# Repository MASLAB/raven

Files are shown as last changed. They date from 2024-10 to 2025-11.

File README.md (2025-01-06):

# raven
Robot Hardware Controller

## Pcb
Color pallet works best with KiCad wDark theme

## Firmware
Built using cmake and all dependencies exist locally

Install build tools if you need to
```
sudo apt install ninja-build cmake gcc-arm-none-eabi
```

### Compiling
Compile from motor-hub folder
```
cmake . --preset=Release
cd Release
ninja
```

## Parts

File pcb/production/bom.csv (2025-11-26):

Designator | Footprint | Quantity | Value | LCSC Part #
C1 | C_Elec_8x6.2 | 1 | 100u | C178539
C10, C18, C30, C31, C34, C35, C36, C39, C7, C8 | 0402 | 10 | 100n | C1525
C11, C44 | 0402 | 2 | 220n | C16772
C12 | 0603 | 1 | 4u7 | C19666
C13, C50, C51, C52, C53, C54, C57, C58, C59, C60, C61, C62, C63, C64, C65 | 0805 | 15 | 22u | C45783
C14, C16, C19, C2, C21, C24, C26, C4, C66, C68 | 0402 | 10 | 100n | C307331
C15, C20, C25, C3, C6, C67, C9 | 0402 | 7 | 2u2 | C12530
C17, C22, C27, C5, C69 | 0402 | 5 | 22n | C1532
C23 | 0603 | 1 | 100n | C14663
C28 | 0603 | 1 | 10u | C96446
C32, C33 | 0402 | 2 | 12p | C1547
C37, C38, C46, C47, C48, C49 | 0402 | 6 | 1u | C52923
C40, C41, C42, C43 | 1206 | 4 | 47u | C96123
C45 | 0805 | 1 | 2u2 | C377773
C55 | 0402 | 1 | 10u | C15525
D1, D12, D14, D27, D3, D6, D9 | 0603 | 7 | GLED | C72043
D10, D13, D28, D4, D7 | 0603 | 5 | RLED | C2286
D11, D2, D26, D5, D8 | 0603 | 5 | WLED | C2290
F1 | 1206 | 1 | Fuse | C2838917
FB1 | 0805 | 1 | FerriteBead | C1017
J2, J5 | JST_SH_SM04B-SRSS-TB_1x04-1MP_P1.00mm_Horizontal | 2 | Conn_01x04_MountingPin | C160404
L1 | L_0660A | 1 | 1u | C18199443
Q1 | SOT-23 | 1 | AO3400A | C20917
Q3 | DMP2002UPS | 1 | DMP2002UPS | C154869
R1, R10, R11, R12, R13, R14, R15, R16, R17, R18, R19, R2, R20, R21, R22, R23, R27, R3, R4, R5, R50, R59, R6, R60, R61, R62, R63, R9 | 0402 | 28 | 1k | C11702
R24 | 0402 | 1 | 33k | C25779
R25, R26, R28, R29, R31, R33, R34, R35, R37, R39, R40, R41, R43, R49, R51, R52, R54, R55, R66, R7, R8 | 0402 | 21 | 7k5 | C25918
R53, R57 | 0402 | 2 | 56k | C25796
R56 | 0402 | 1 | 47k | C25792
R58 | 0402 | 1 | 100k | C25741
SW1, SW2 | TS-1088 | 2 | SW_Push | C720477
U1, U30, U4, U5, U6 | HTSSOP-16-1EP_4.4x5mm_P0.65mm_EP3.4x5mm_Mask2.46x2.31mm | 5 | DRV8874PWPR | C1855818
U2 | LGA-14_3x2.5mm_P0.5mm_LayoutBorder3x4y | 1 | ICM-42688-P | C1850418
U7 | QFN-48-1EP_7x7mm_P0.5mm_EP5.6x5.6mm | 1 | STM32G431CBUx | C529356
U8 | SOIC-16_3.9x9.9mm_P1.27mm | 1 | 74HC595 | C5947
U9 | TPS548B28RWWR | 1 | TPS548B28RWWR | C3188716
Y1 | Crystal_SMD_3225-4Pin_3.2x2.5mm | 1 | 16MHz | C13738

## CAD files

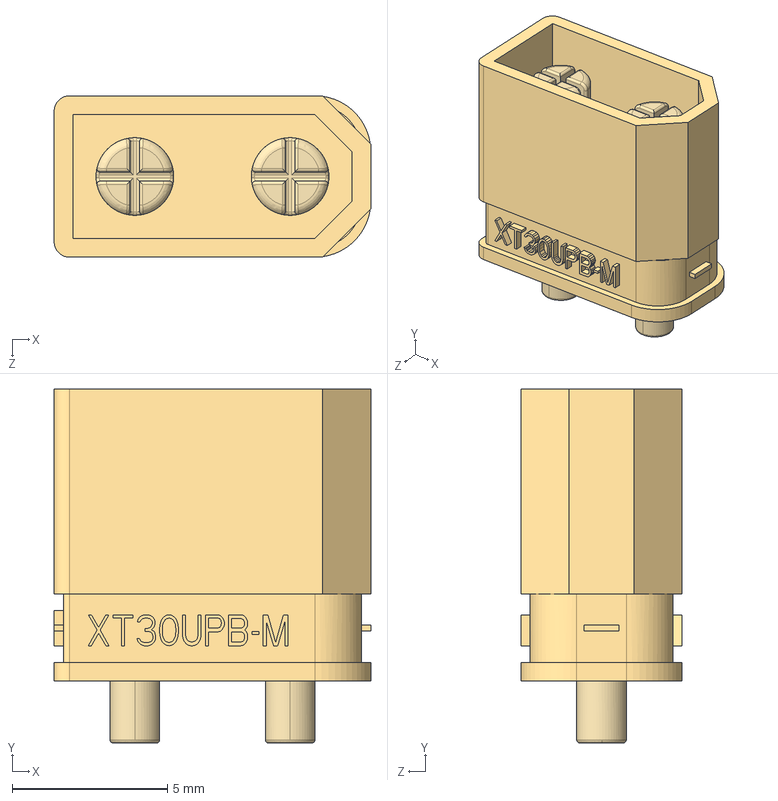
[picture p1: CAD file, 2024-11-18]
pcb/3dmodels/XT30UPB-M.STEP
10.2 x 11.4 x 5.20 mm
XT30UPB-M
XT30UPB-M-PIN x 2

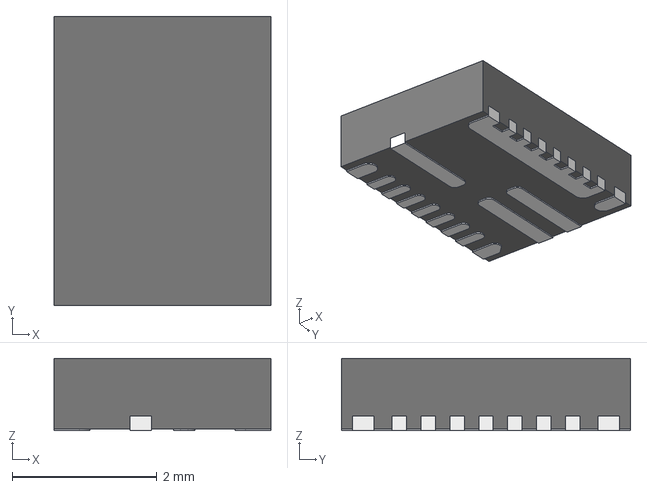
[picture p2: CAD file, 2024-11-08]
pcb/3dmodels/RWW0021A.STEP
3.00 x 4.00 x 1.00 mm
FRAME
MOLD

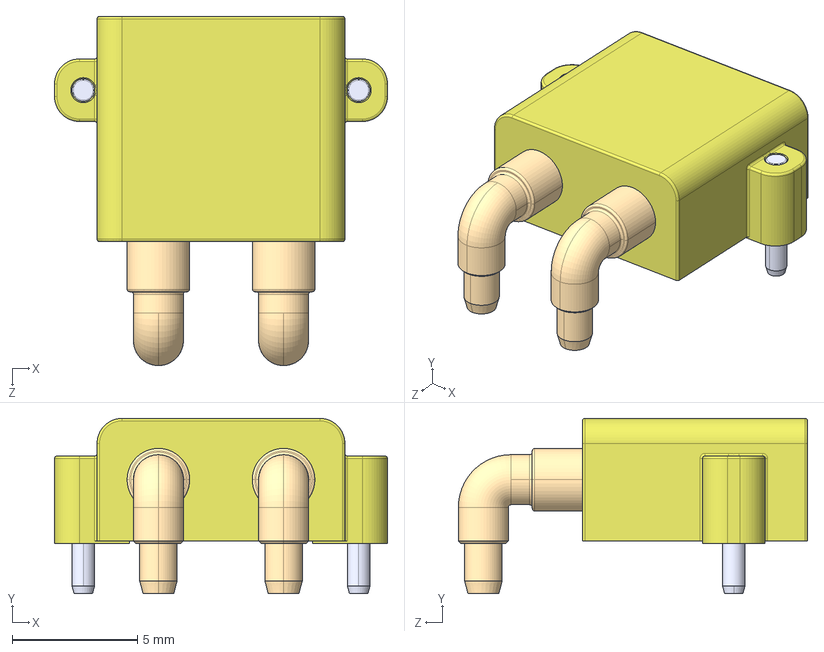
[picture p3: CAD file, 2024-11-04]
pcb/3dmodels/XT30PW-M.STEP
13.3 x 7.00 x 14.0 mm

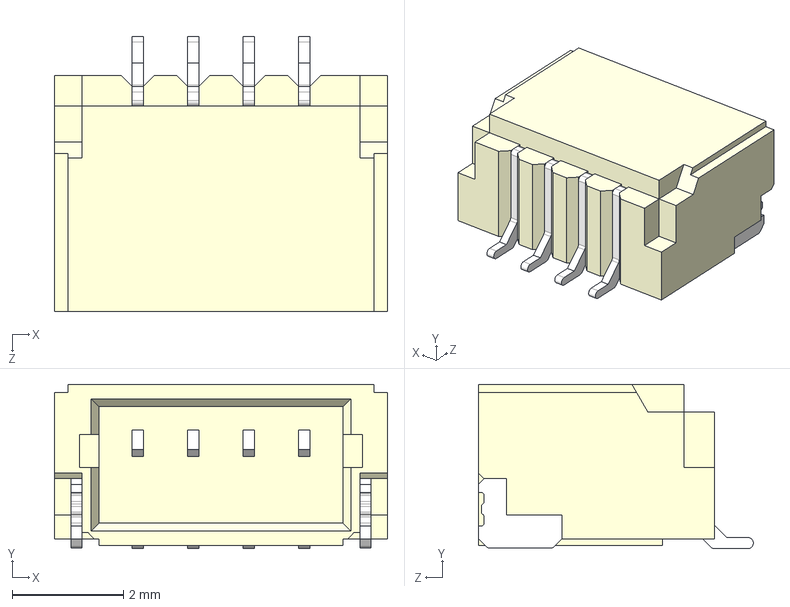
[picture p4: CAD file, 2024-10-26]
pcb/3dmodels/SM04B-SRSS-TB.STEP
6.00 x 2.96 x 4.95 mm

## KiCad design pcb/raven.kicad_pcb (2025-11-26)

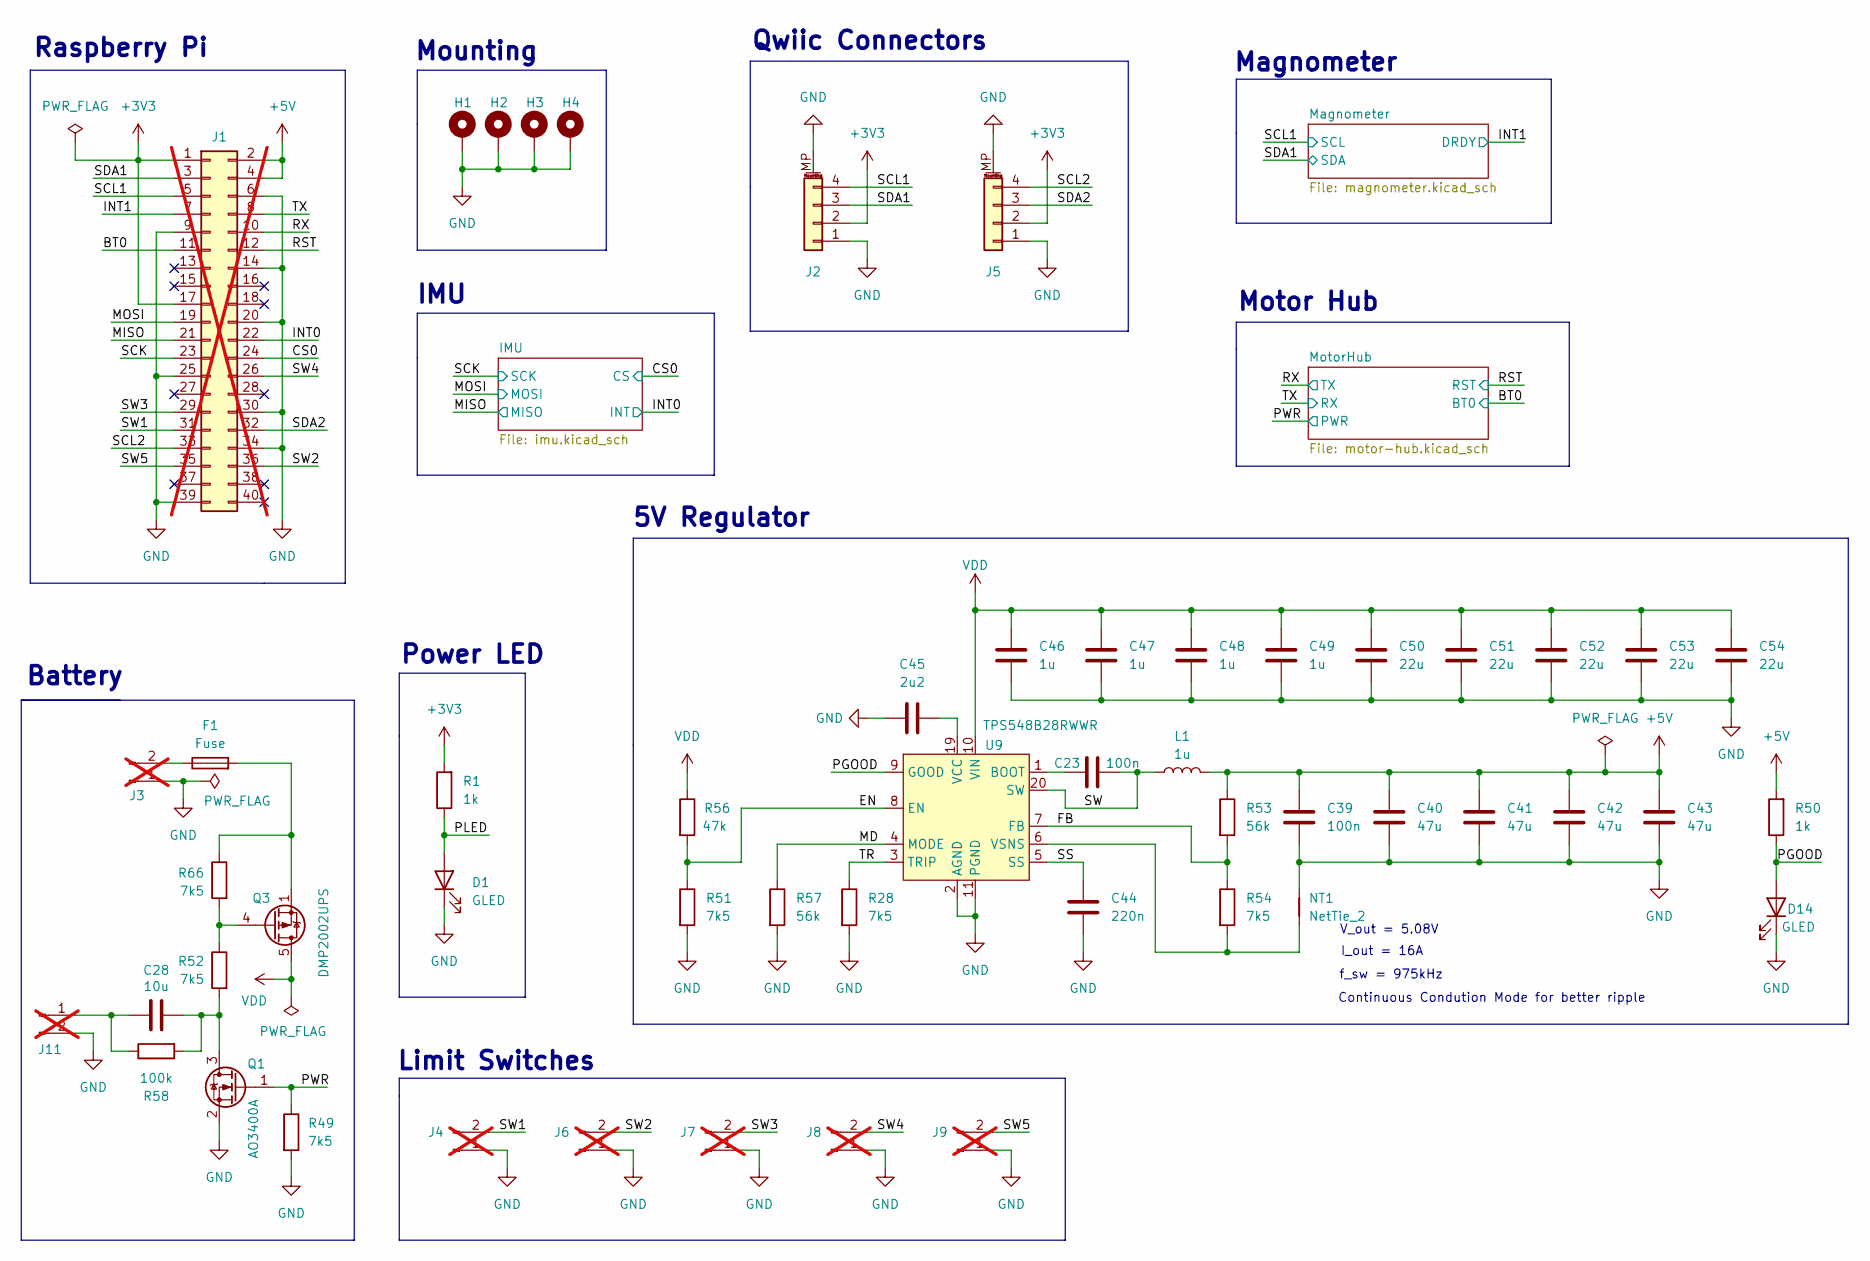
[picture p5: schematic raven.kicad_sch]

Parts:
C23: 100n; C_0603_1608Metric; LCSC C14663
C28: 10u; C_0603_1608Metric; LCSC C96446
C39: 100n; C_0402_1005Metric; LCSC C1525
C40, C41, C42, C43: 47u; C_1206_3216Metric; LCSC C96123
C44: 220n; C_0402_1005Metric; LCSC C16772
C45: 2u2; C_0805_2012Metric; LCSC C377773
C46, C47, C48, C49: 1u; C_0402_1005Metric; LCSC C52923
C50, C51, C52, C53, C54: 22u; C_0805_2012Metric; LCSC C45783
D1, D14: GLED; LED_0603_1608Metric; LCSC C72043
F1: Fuse; Fuse_1206_3216Metric; LCSC C2838917
H1, H2, H3, H4: MountingHole_Pad; MountingHole_2.5mm_Pad
J1: Conn_02x20_Odd_Even; PinSocket_2x20_P2.54mm_Vertical; LCSC C35165; not fitted
J2, J5: Conn_01x04_MountingPin; JST_SH_SM04B-SRSS-TB_1x04-1MP_P1.00mm_Horizontal; LCSC C160404
J3: Conn_01x02_Pin; AMASS_XT30UPB-M_1x02_P5.0mm_Vertical; LCSC C428721; not fitted
J4, J6, J7, J8, J9: Conn_01x02_Pin; PinHeader_1x02_P2.54mm_Vertical; LCSC C492401; not fitted
J11: Conn_01x02_Pin; JST_PH_B2B-PH-K_1x02_P2.00mm_Vertical; LCSC C131337; not fitted
L1: 1u; L_0660A; LCSC C18199443
NT1: NetTie_2; NetTie-2_SMD_Pad0.5mm
Q1: AO3400A; SOT-23; LCSC C20917
Q3: DMP2002UPS; LCSC C154869
R1, R50: 1k; R_0402_1005Metric; LCSC C11702
R28, R49, R51, R52, R54, R66: 7k5; R_0402_1005Metric; LCSC C25918
R53, R57: 56k; R_0402_1005Metric; LCSC C25796
R56: 47k; R_0402_1005Metric; LCSC C25792
R58: 100k; R_0402_1005Metric; LCSC C25741
U9: TPS548B28RWWR; LCSC C3188716

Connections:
+3V3: J1.1, J1.17, J2.2, J5.2, R1.2; also elsewhere on the board
+5V: C39.2, C40.1, C41.1, C42.1, C43.1, J1.2, J1.4, L1.2, R50.2, R53.1; also elsewhere on the board
/BT0: J1.11; also elsewhere on the board
/CS0: J1.24; also elsewhere on the board
/EN: R51.1, R56.2, U9.8 (EN)
/FB: R53.2, R54.1, U9.7 (FB)
/INT0: J1.22; also elsewhere on the board
/INT1: J1.7; also elsewhere on the board
/MD: R57.1, U9.4 (MODE)
/MISO: J1.21; also elsewhere on the board
/MOSI: J1.19; also elsewhere on the board
/PGOOD: D14.2 (A), R50.1, U9.9 (GOOD)
/PLED: D1.2 (A), R1.1
/PWR: Q1.1 (G), R49.1; also elsewhere on the board
/RST: J1.12; also elsewhere on the board
/RX: J1.10; also elsewhere on the board
/SCK: J1.23; also elsewhere on the board
/SCL1: J1.5, J2.4; also elsewhere on the board
/SCL2: J1.33, J5.4
/SDA1: J1.3, J2.3; also elsewhere on the board
/SDA2: J1.32, J5.3
/SS: C44.1, U9.5 (SS)
/SW: C23.2, L1.1, U9.20 (SW)
/SW1: J1.31, J4.2
/SW2: J1.36, J6.2
/SW3: J1.29, J7.2
/SW4: J1.26, J8.2
/SW5: J1.35, J9.2
/TR: R28.1, U9.3 (TRIP)
/TX: J1.8; also elsewhere on the board
GND: C39.1, C40.2, C41.2, C42.2, C43.2, C44.2, C45.1, C46.2, C47.2, C48.2, C49.2, C50.2, C51.2, C52.2, C53.2, C54.2, D1.1 (K), D14.1 (K), H1.1, H2.1, H3.1, H4.1, J1.6, J1.9, J1.14, J1.20, J1.25, J1.30, J1.34, J1.39, J2.1, J2.MP (MountPin), J3.1, J4.1, J5.1, J5.MP (MountPin), J6.1, J7.1, J8.1, J9.1, J11.2, NT1.1, Q1.2 (S), R28.2, R49.2, R51.2, R57.2, U9.2 (AGND), U9.11 (PGND), U9.12 (PGND), U9.13 (PGND), U9.14 (PGND), U9.15 (PGND), U9.16 (PGND), U9.17 (PGND), U9.18 (PGND); also elsewhere on the board
unnamed: F1.2, Q3.1 (S), Q3.2 (S), Q3.3 (S), R66.1
unnamed: F1.1, J3.2
unnamed: C28.1, J11.1, R58.1
unnamed: C28.2, Q1.3 (D), R52.2, R58.2
unnamed: Q3.4 (G), R52.1, R66.2
unnamed: C23.1, U9.1 (BOOT)
unnamed: C45.2, U9.19 (VCC)
unnamed: NT1.2, R54.2, U9.6 (VSNS)
VDD: C46.1, C47.1, C48.1, C49.1, C50.1, C51.1, C52.1, C53.1, C54.1, Q3.5 (D), Q3.6 (D), Q3.7 (D), Q3.8 (D), R56.1, U9.10 (VIN), U9.21 (VIN); also elsewhere on the board

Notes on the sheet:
Mounting
Power LED
5V Regulator
IMU
Motor Hub
V_out = 5.08V
Limit Switches
Continuous Condution Mode for better ripple
Qwiic Connectors
Battery
I_out = 16A
f_sw = 975kHz
Raspberry Pi
Magnometer

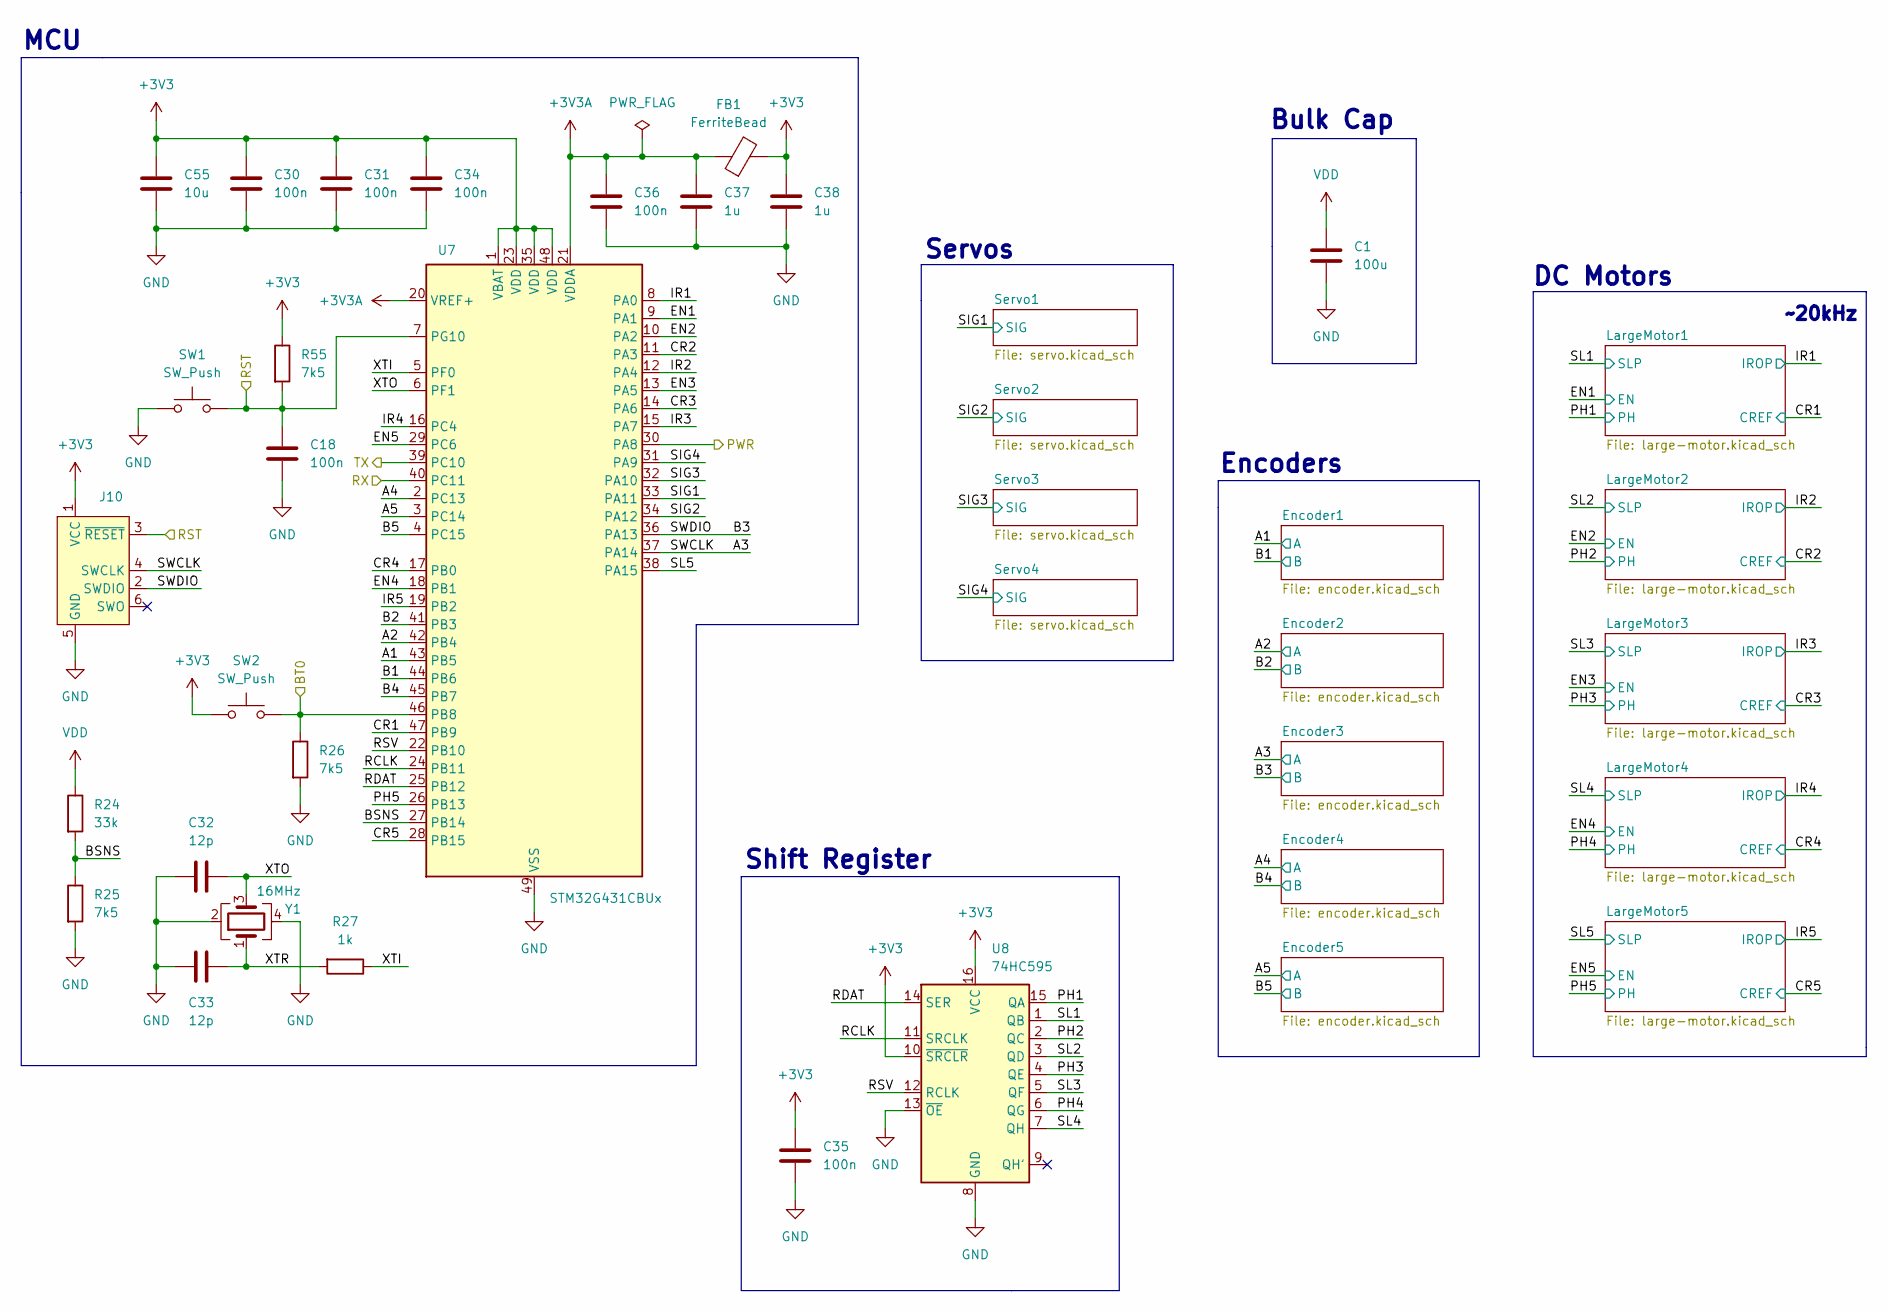
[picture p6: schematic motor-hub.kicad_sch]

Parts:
C1: 100u; C_Elec_8x6.2; LCSC C178539
C18, C30, C31, C34, C35, C36: 100n; C_0402_1005Metric; LCSC C1525
C32, C33: 12p; C_0402_1005Metric; LCSC C1547
C37, C38: 1u; C_0402_1005Metric; LCSC C52923
C55: 10u; C_0402_1005Metric; LCSC C15525
FB1: FerriteBead; L_0805_2012Metric; LCSC C1017
J10: Conn_ARM_SWD_TagConnect_TC2030-NL; Tag-Connect_TC2030-IDC-NL_2x03_P1.27mm_Vertical
R24: 33k; R_0402_1005Metric; LCSC C25779
R25, R26, R55: 7k5; R_0402_1005Metric; LCSC C25918
R27: 1k; R_0402_1005Metric; LCSC C11702
SW1, SW2: SW_Push; TS-1088; LCSC C720477
U7: STM32G431CBUx; QFN-48-1EP_7x7mm_P0.5mm_EP5.6x5.6mm; LCSC C529356
U8: 74HC595; SOIC-16_3.9x9.9mm_P1.27mm; LCSC C5947
Y1: 16MHz; Crystal_SMD_3225-4Pin_3.2x2.5mm; LCSC C13738

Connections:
+3V3: C30.1, C31.1, C34.1, C35.1, C38.1, C55.1, FB1.2, J10.1 (VCC), R55.1, SW2.1, U7.1 (VBAT), U7.23 (VDD), U7.35 (VDD), U7.48 (VDD), U8.10 (~SRCLR), U8.16 (VCC); also elsewhere on the board
+3V3A: C36.1, C37.1, FB1.1, U7.20 (VREF+), U7.21 (VDDA)
/BT0: R26.1, SW2.2, U7.46 (PB8); also elsewhere on the board
/MotorHub/A1: U7.43 (PB5); also elsewhere on the board
/MotorHub/A2: U7.42 (PB4); also elsewhere on the board
/MotorHub/A3: J10.4 (SWCLK), U7.37 (PA14); also elsewhere on the board
/MotorHub/A4: U7.2 (PC13); also elsewhere on the board
/MotorHub/A5: U7.3 (PC14); also elsewhere on the board
/MotorHub/B1: U7.44 (PB6); also elsewhere on the board
/MotorHub/B2: U7.41 (PB3); also elsewhere on the board
/MotorHub/B3: J10.2 (SWDIO), U7.36 (PA13); also elsewhere on the board
/MotorHub/B4: U7.45 (PB7); also elsewhere on the board
/MotorHub/B5: U7.4 (PC15); also elsewhere on the board
/MotorHub/BSNS: R24.2, R25.1, U7.27 (PB14)
/MotorHub/CR1: U7.47 (PB9); also elsewhere on the board
/MotorHub/CR2: U7.11 (PA3); also elsewhere on the board
/MotorHub/CR3: U7.14 (PA6); also elsewhere on the board
/MotorHub/CR4: U7.17 (PB0); also elsewhere on the board
/MotorHub/CR5: U7.28 (PB15); also elsewhere on the board
/MotorHub/EN1: U7.9 (PA1); also elsewhere on the board
/MotorHub/EN2: U7.10 (PA2); also elsewhere on the board
/MotorHub/EN3: U7.13 (PA5); also elsewhere on the board
/MotorHub/EN4: U7.18 (PB1); also elsewhere on the board
/MotorHub/EN5: U7.29 (PC6); also elsewhere on the board
/MotorHub/IR1: U7.8 (PA0); also elsewhere on the board
/MotorHub/IR2: U7.12 (PA4); also elsewhere on the board
/MotorHub/IR3: U7.15 (PA7); also elsewhere on the board
/MotorHub/IR4: U7.16 (PC4); also elsewhere on the board
/MotorHub/IR5: U7.19 (PB2); also elsewhere on the board
/MotorHub/PH1: U8.15 (QA); also elsewhere on the board
/MotorHub/PH2: U8.2 (QC); also elsewhere on the board
/MotorHub/PH3: U8.4 (QE); also elsewhere on the board
/MotorHub/PH4: U8.6 (QG); also elsewhere on the board
/MotorHub/PH5: U7.26 (PB13); also elsewhere on the board
/MotorHub/RCLK: U7.24 (PB11), U8.11 (SRCLK)
/MotorHub/RDAT: U7.25 (PB12), U8.14 (SER)
/MotorHub/RSV: U7.22 (PB10), U8.12 (RCLK)
/MotorHub/SIG1: U7.33 (PA11); also elsewhere on the board
/MotorHub/SIG2: U7.34 (PA12); also elsewhere on the board
/MotorHub/SIG3: U7.32 (PA10); also elsewhere on the board
/MotorHub/SIG4: U7.31 (PA9); also elsewhere on the board
/MotorHub/SL1: U8.1 (QB); also elsewhere on the board
/MotorHub/SL2: U8.3 (QD); also elsewhere on the board
/MotorHub/SL3: U8.5 (QF); also elsewhere on the board
/MotorHub/SL4: U8.7 (QH); also elsewhere on the board
/MotorHub/SL5: U7.38 (PA15); also elsewhere on the board
/MotorHub/XTI: R27.1, U7.5 (PF0)
/MotorHub/XTO: C32.2, U7.6 (PF1), Y1.3
/MotorHub/XTR: C33.2, R27.2, Y1.1
/PWR: U7.30 (PA8); also elsewhere on the board
/RST: C18.1, J10.3 (~RESET), R55.2, SW1.2, U7.7 (PG10); also elsewhere on the board
/RX: U7.39 (PC10); also elsewhere on the board
/TX: U7.40 (PC11); also elsewhere on the board
GND: C1.2, C18.2, C30.2, C31.2, C32.1, C33.1, C34.2, C35.2, C36.2, C37.2, C38.2, C55.2, J10.5 (GND), R25.2, R26.2, SW1.1, U7.49 (VSS), U8.8 (GND), U8.13 (~OE), Y1.2, Y1.4; also elsewhere on the board
VDD: C1.1, R24.1; also elsewhere on the board

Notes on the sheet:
~20kHz
Bulk Cap
Servos
MCU
DC Motors
Encoders
Shift Register

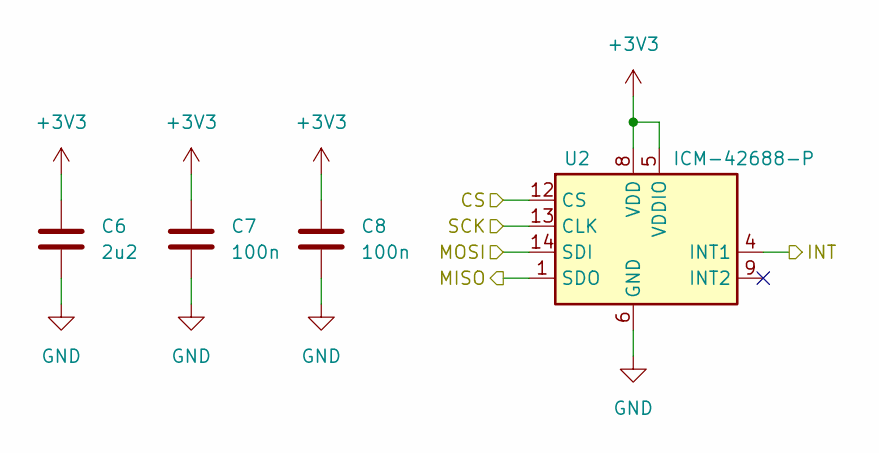
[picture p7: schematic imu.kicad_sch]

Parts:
C6: 2u2; C_0402_1005Metric; LCSC C12530
C7, C8: 100n; C_0402_1005Metric; LCSC C1525
U2: ICM-42688-P; LGA-14_3x2.5mm_P0.5mm_LayoutBorder3x4y; LCSC C1850418

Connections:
+3V3: C6.1, C7.1, C8.1, U2.5 (VDDIO), U2.8 (VDD); also elsewhere on the board
/CS0: U2.12 (CS); also elsewhere on the board
/INT0: U2.4 (INT1); also elsewhere on the board
/MISO: U2.1 (SDO); also elsewhere on the board
/MOSI: U2.14 (SDI); also elsewhere on the board
/SCK: U2.13 (CLK); also elsewhere on the board
GND: C6.2, C7.2, C8.2, U2.6 (GND), U2.7 (RESV), U2.11 (RESV); also elsewhere on the board

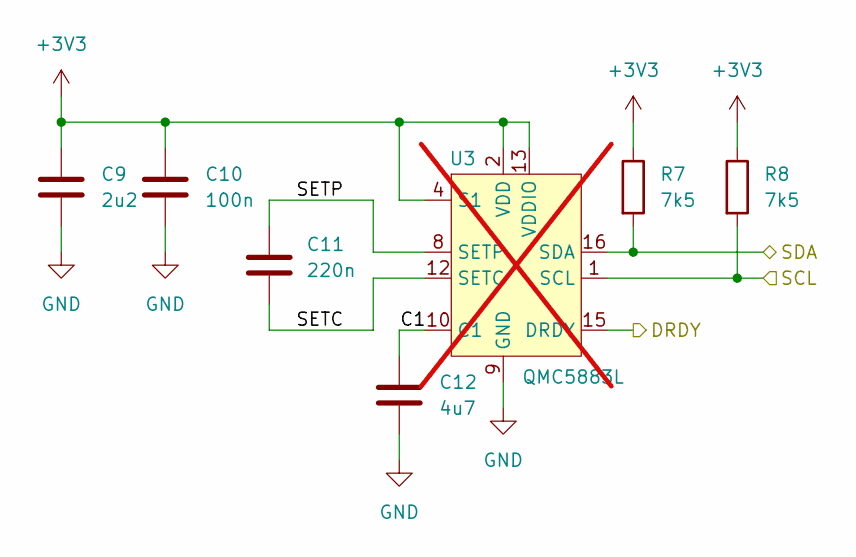
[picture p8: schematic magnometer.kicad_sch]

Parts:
C9: 2u2; C_0402_1005Metric; LCSC C12530
C10: 100n; C_0402_1005Metric; LCSC C1525
C11: 220n; C_0402_1005Metric; LCSC C16772
C12: 4u7; C_0603_1608Metric; LCSC C19666
R7, R8: 7k5; R_0402_1005Metric; LCSC C25918
U3: QMC5883L; LGA-16_3x3mm_P0.5mm; not fitted

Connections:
+3V3: C9.1, C10.1, R7.1, R8.1, U3.2 (VDD), U3.4 (S1), U3.13 (VDDIO); also elsewhere on the board
/INT1: U3.15 (DRDY); also elsewhere on the board
/Magnometer/C1: C12.1, U3.10 (C1)
/Magnometer/SETC: C11.2, U3.12 (SETC)
/Magnometer/SETP: C11.1, U3.8 (SETP)
/SCL1: R8.2, U3.1 (SCL); also elsewhere on the board
/SDA1: R7.2, U3.16 (SDA); also elsewhere on the board
GND: C9.2, C10.2, C12.2, U3.9 (GND), U3.11 (GND); also elsewhere on the board

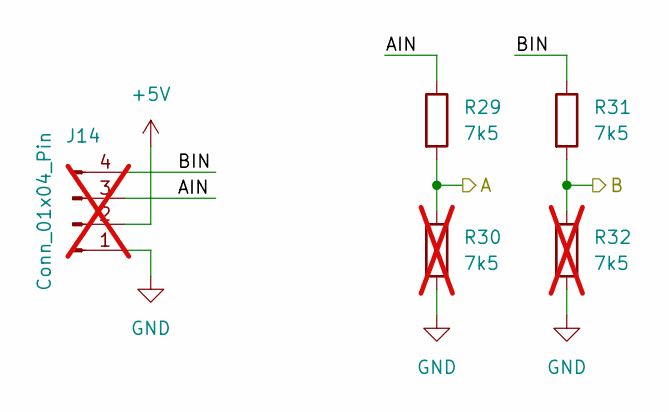
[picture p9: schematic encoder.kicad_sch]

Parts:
J14: Conn_01x04_Pin; PinHeader_1x04_P2.54mm_Vertical; LCSC C6332197; not fitted
R29, R31: 7k5; R_0402_1005Metric; LCSC C25918
R30, R32: 7k5; R_0402_1005Metric; LCSC C25918; not fitted

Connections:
+5V: J14.2; also elsewhere on the board
/MotorHub/A1: R29.2, R30.1; also elsewhere on the board
/MotorHub/B1: R31.2, R32.1; also elsewhere on the board
/MotorHub/Encoder1/AIN: J14.3, R29.1
/MotorHub/Encoder1/BIN: J14.4, R31.1
GND: J14.1, R30.2, R32.2; also elsewhere on the board

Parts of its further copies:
J15, J16, J17, J18: Conn_01x04_Pin; PinHeader_1x04_P2.54mm_Vertical; LCSC C6332197; not fitted
R33, R34, R35, R37, R39, R40, R41, R43: 7k5; R_0402_1005Metric; LCSC C25918
R36, R38, R42, R44, R45, R46, R47, R48: 7k5; R_0402_1005Metric; LCSC C25918; not fitted

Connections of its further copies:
+5V: J15.2, J16.2, J17.2, J18.2; also elsewhere on the board
/MotorHub/A2: R33.2, R36.1; also elsewhere on the board
/MotorHub/A3: R34.2, R42.1; also elsewhere on the board
/MotorHub/A4: R35.2, R47.1; also elsewhere on the board
/MotorHub/A5: R39.2, R48.1; also elsewhere on the board
/MotorHub/B2: R37.2, R38.1; also elsewhere on the board
/MotorHub/B3: R40.2, R44.1; also elsewhere on the board
/MotorHub/B4: R41.2, R45.1; also elsewhere on the board
/MotorHub/B5: R43.2, R46.1; also elsewhere on the board
/MotorHub/Encoder2/AIN: J15.3, R33.1
/MotorHub/Encoder2/BIN: J15.4, R37.1
/MotorHub/Encoder3/AIN: J16.3, R34.1
/MotorHub/Encoder3/BIN: J16.4, R40.1
/MotorHub/Encoder4/AIN: J17.3, R35.1
/MotorHub/Encoder4/BIN: J17.4, R41.1
/MotorHub/Encoder5/AIN: J18.3, R39.1
/MotorHub/Encoder5/BIN: J18.4, R43.1
GND: J15.1, J16.1, J17.1, J18.1, R36.2, R38.2, R42.2, R44.2, R45.2, R46.2, R47.2, R48.2; also elsewhere on the board

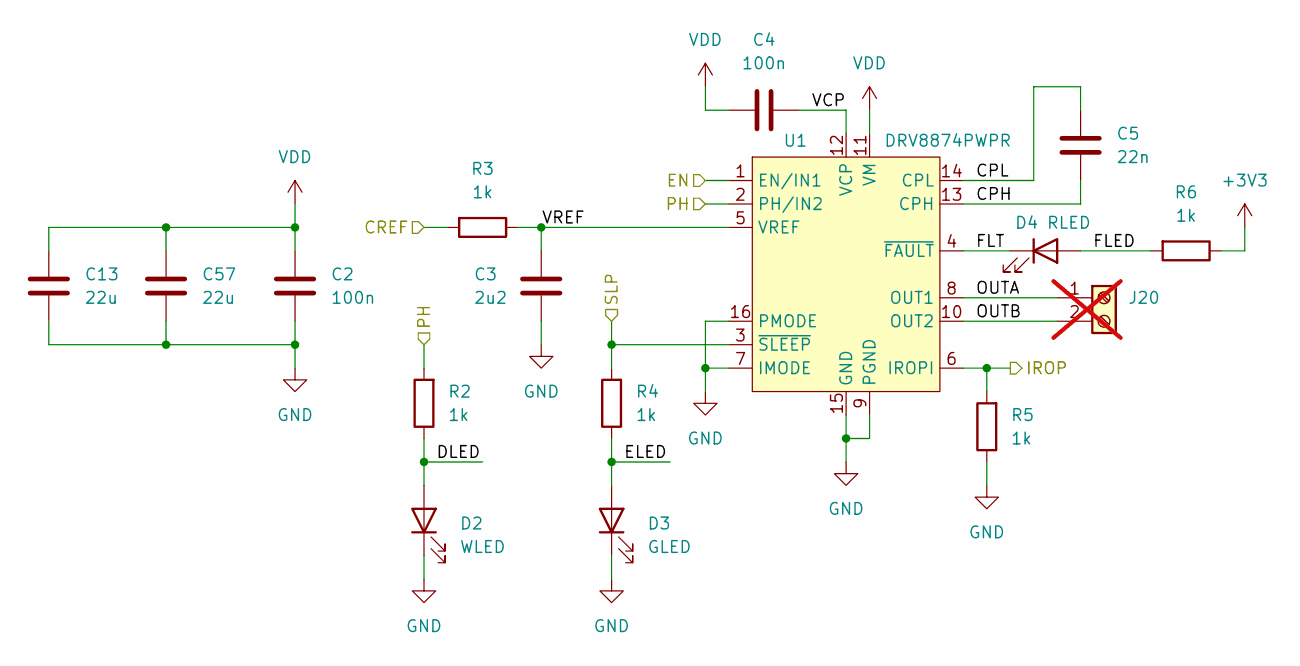
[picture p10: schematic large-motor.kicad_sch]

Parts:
C2, C4: 100n; C_0402_1005Metric; LCSC C307331
C3: 2u2; C_0402_1005Metric; LCSC C12530
C5: 22n; C_0402_1005Metric; LCSC C1532
C13, C57: 22u; C_0805_2012Metric; LCSC C45783
D2: WLED; LED_0603_1608Metric; LCSC C2290
D3: GLED; LED_0603_1608Metric; LCSC C72043
D4: RLED; LED_0603_1608Metric; LCSC C2286
J20: Screw_Terminal_01x02; TerminalBlock_Phoenix_MKDS-1,5-2_1x02_P5.00mm_Horizontal; LCSC C8404; not fitted
R2, R3, R4, R5, R6: 1k; R_0402_1005Metric; LCSC C11702
U1: DRV8874PWPR; HTSSOP-16-1EP_4.4x5mm_P0.65mm_EP3.4x5mm_Mask2.46x2.31mm; LCSC C1855818

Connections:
+3V3: R6.1; also elsewhere on the board
/MotorHub/CR2: R3.2; also elsewhere on the board
/MotorHub/EN2: U1.1 (EN/IN1); also elsewhere on the board
/MotorHub/IR2: R5.2, U1.6 (IROPI); also elsewhere on the board
/MotorHub/LargeMotor2/CPH: C5.2, U1.13 (CPH)
/MotorHub/LargeMotor2/CPL: C5.1, U1.14 (CPL)
/MotorHub/LargeMotor2/DLED: D2.2 (A), R2.1
/MotorHub/LargeMotor2/ELED: D3.2 (A), R4.1
/MotorHub/LargeMotor2/FLED: D4.2 (A), R6.2
/MotorHub/LargeMotor2/FLT: D4.1 (K), U1.4 (~FAULT)
/MotorHub/LargeMotor2/OUTA: J20.1, U1.8 (OUT1)
/MotorHub/LargeMotor2/OUTB: J20.2, U1.10 (OUT2)
/MotorHub/LargeMotor2/VCP: C4.2, U1.12 (VCP)
/MotorHub/LargeMotor2/VREF: C3.1, R3.1, U1.5 (VREF)
/MotorHub/PH2: R2.2, U1.2 (PH/IN2); also elsewhere on the board
/MotorHub/SL2: R4.2, U1.3 (~SLEEP); also elsewhere on the board
GND: C2.2, C3.2, C13.2, C57.2, D2.1 (K), D3.1 (K), R5.1, U1.7 (IMODE), U1.9 (PGND), U1.15 (GND), U1.16 (PMODE), U1.17 (PAD); also elsewhere on the board
VDD: C2.1, C4.1, C13.1, C57.1, U1.11 (VM); also elsewhere on the board

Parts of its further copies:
C14, C16, C19, C21, C24, C26, C66, C68: 100n; C_0402_1005Metric; LCSC C307331
C15, C20, C25, C67: 2u2; C_0402_1005Metric; LCSC C12530
C17, C22, C27, C69: 22n; C_0402_1005Metric; LCSC C1532
C58, C59, C60, C61, C62, C63, C64, C65: 22u; C_0805_2012Metric; LCSC C45783
D5, D8, D11, D26: WLED; LED_0603_1608Metric; LCSC C2290
D6, D9, D12, D27: GLED; LED_0603_1608Metric; LCSC C72043
D7, D10, D13, D28: RLED; LED_0603_1608Metric; LCSC C2286
J26, J27, J28, J29: Screw_Terminal_01x02; TerminalBlock_Phoenix_MKDS-1,5-2_1x02_P5.00mm_Horizontal; LCSC C8404; not fitted
R9, R10, R11, R12, R13, R14, R15, R16, R17, R18, R19, R20, R21, R22, R23, R59, R60, R61, R62, R63: 1k; R_0402_1005Metric; LCSC C11702
U4, U5, U6, U30: DRV8874PWPR; HTSSOP-16-1EP_4.4x5mm_P0.65mm_EP3.4x5mm_Mask2.46x2.31mm; LCSC C1855818

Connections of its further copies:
+3V3: R13.1, R18.1, R23.1, R63.1; also elsewhere on the board
/MotorHub/CR1: R60.2; also elsewhere on the board
/MotorHub/CR3: R10.2; also elsewhere on the board
/MotorHub/CR4: R15.2; also elsewhere on the board
/MotorHub/CR5: R20.2; also elsewhere on the board
/MotorHub/EN1: U30.1 (EN/IN1); also elsewhere on the board
/MotorHub/EN3: U4.1 (EN/IN1); also elsewhere on the board
/MotorHub/EN4: U5.1 (EN/IN1); also elsewhere on the board
/MotorHub/EN5: U6.1 (EN/IN1); also elsewhere on the board
/MotorHub/IR1: R62.2, U30.6 (IROPI); also elsewhere on the board
/MotorHub/IR3: R12.2, U4.6 (IROPI); also elsewhere on the board
/MotorHub/IR4: R17.2, U5.6 (IROPI); also elsewhere on the board
/MotorHub/IR5: R22.2, U6.6 (IROPI); also elsewhere on the board
/MotorHub/LargeMotor1/CPH: C69.2, U30.13 (CPH)
/MotorHub/LargeMotor1/CPL: C69.1, U30.14 (CPL)
/MotorHub/LargeMotor1/DLED: D26.2 (A), R59.1
/MotorHub/LargeMotor1/ELED: D27.2 (A), R61.1
/MotorHub/LargeMotor1/FLED: D28.2 (A), R63.2
/MotorHub/LargeMotor1/FLT: D28.1 (K), U30.4 (~FAULT)
/MotorHub/LargeMotor1/OUTA: J29.1, U30.8 (OUT1)
/MotorHub/LargeMotor1/OUTB: J29.2, U30.10 (OUT2)
/MotorHub/LargeMotor1/VCP: C68.2, U30.12 (VCP)
/MotorHub/LargeMotor1/VREF: C67.1, R60.1, U30.5 (VREF)
/MotorHub/LargeMotor3/CPH: C17.2, U4.13 (CPH)
/MotorHub/LargeMotor3/CPL: C17.1, U4.14 (CPL)
/MotorHub/LargeMotor3/DLED: D5.2 (A), R9.1
/MotorHub/LargeMotor3/ELED: D6.2 (A), R11.1
/MotorHub/LargeMotor3/FLED: D7.2 (A), R13.2
/MotorHub/LargeMotor3/FLT: D7.1 (K), U4.4 (~FAULT)
/MotorHub/LargeMotor3/OUTA: J26.1, U4.8 (OUT1)
/MotorHub/LargeMotor3/OUTB: J26.2, U4.10 (OUT2)
/MotorHub/LargeMotor3/VCP: C16.2, U4.12 (VCP)
/MotorHub/LargeMotor3/VREF: C15.1, R10.1, U4.5 (VREF)
/MotorHub/LargeMotor4/CPH: C22.2, U5.13 (CPH)
/MotorHub/LargeMotor4/CPL: C22.1, U5.14 (CPL)
/MotorHub/LargeMotor4/DLED: D8.2 (A), R14.1
/MotorHub/LargeMotor4/ELED: D9.2 (A), R16.1
/MotorHub/LargeMotor4/FLED: D10.2 (A), R18.2
/MotorHub/LargeMotor4/FLT: D10.1 (K), U5.4 (~FAULT)
/MotorHub/LargeMotor4/OUTA: J27.1, U5.8 (OUT1)
/MotorHub/LargeMotor4/OUTB: J27.2, U5.10 (OUT2)
/MotorHub/LargeMotor4/VCP: C21.2, U5.12 (VCP)
/MotorHub/LargeMotor4/VREF: C20.1, R15.1, U5.5 (VREF)
/MotorHub/LargeMotor5/CPH: C27.2, U6.13 (CPH)
/MotorHub/LargeMotor5/CPL: C27.1, U6.14 (CPL)
/MotorHub/LargeMotor5/DLED: D11.2 (A), R19.1
/MotorHub/LargeMotor5/ELED: D12.2 (A), R21.1
/MotorHub/LargeMotor5/FLED: D13.2 (A), R23.2
/MotorHub/LargeMotor5/FLT: D13.1 (K), U6.4 (~FAULT)
/MotorHub/LargeMotor5/OUTA: J28.1, U6.8 (OUT1)
/MotorHub/LargeMotor5/OUTB: J28.2, U6.10 (OUT2)
/MotorHub/LargeMotor5/VCP: C26.2, U6.12 (VCP)
/MotorHub/LargeMotor5/VREF: C25.1, R20.1, U6.5 (VREF)
/MotorHub/PH1: R59.2, U30.2 (PH/IN2); also elsewhere on the board
/MotorHub/PH3: R9.2, U4.2 (PH/IN2); also elsewhere on the board
/MotorHub/PH4: R14.2, U5.2 (PH/IN2); also elsewhere on the board
/MotorHub/PH5: R19.2, U6.2 (PH/IN2); also elsewhere on the board
/MotorHub/SL1: R61.2, U30.3 (~SLEEP); also elsewhere on the board
/MotorHub/SL3: R11.2, U4.3 (~SLEEP); also elsewhere on the board
/MotorHub/SL4: R16.2, U5.3 (~SLEEP); also elsewhere on the board
/MotorHub/SL5: R21.2, U6.3 (~SLEEP); also elsewhere on the board
GND: C14.2, C15.2, C19.2, C20.2, C24.2, C25.2, C58.2, C59.2, C60.2, C61.2, C62.2, C63.2, C64.2, C65.2, C66.2, C67.2, D5.1 (K), D6.1 (K), D8.1 (K), D9.1 (K), D11.1 (K), D12.1 (K), D26.1 (K), D27.1 (K), R12.1, R17.1, R22.1, R62.1, U4.7 (IMODE), U4.9 (PGND), U4.15 (GND), U4.16 (PMODE), U4.17 (PAD), U5.7 (IMODE), U5.9 (PGND), U5.15 (GND), U5.16 (PMODE), U5.17 (PAD), U6.7 (IMODE), U6.9 (PGND), U6.15 (GND), U6.16 (PMODE), U6.17 (PAD), U30.7 (IMODE), U30.9 (PGND), U30.15 (GND), U30.16 (PMODE), U30.17 (PAD); also elsewhere on the board
VDD: C14.1, C16.1, C19.1, C21.1, C24.1, C26.1, C58.1, C59.1, C60.1, C61.1, C62.1, C63.1, C64.1, C65.1, C66.1, C68.1, U4.11 (VM), U5.11 (VM), U6.11 (VM), U30.11 (VM); also elsewhere on the board

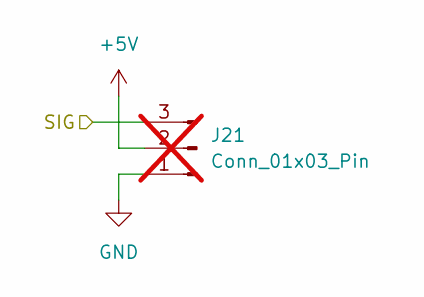
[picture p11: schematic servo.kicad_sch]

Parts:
J21: Conn_01x03_Pin; PinHeader_1x03_P2.54mm_Vertical; LCSC C6332196; not fitted

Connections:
+5V: J21.2; also elsewhere on the board
/MotorHub/SIG1: J21.3; also elsewhere on the board
GND: J21.1; also elsewhere on the board

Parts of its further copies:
J22, J23, J24: Conn_01x03_Pin; PinHeader_1x03_P2.54mm_Vertical; LCSC C6332196; not fitted

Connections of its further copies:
+5V: J22.2, J23.2, J24.2; also elsewhere on the board
/MotorHub/SIG2: J22.3; also elsewhere on the board
/MotorHub/SIG3: J23.3; also elsewhere on the board
/MotorHub/SIG4: J24.3; also elsewhere on the board
GND: J22.1, J23.1, J24.1; also elsewhere on the board

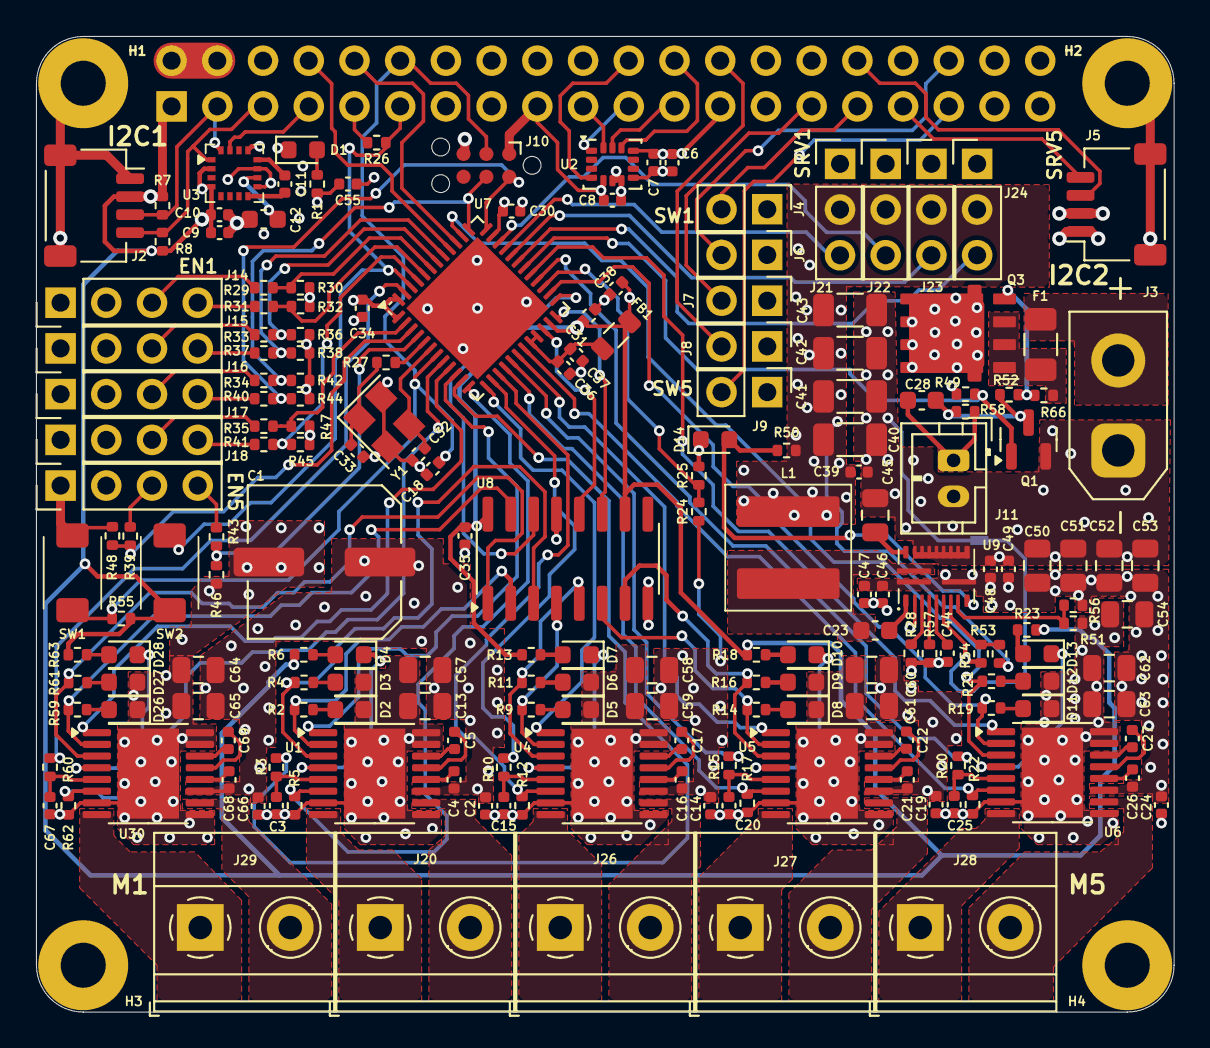
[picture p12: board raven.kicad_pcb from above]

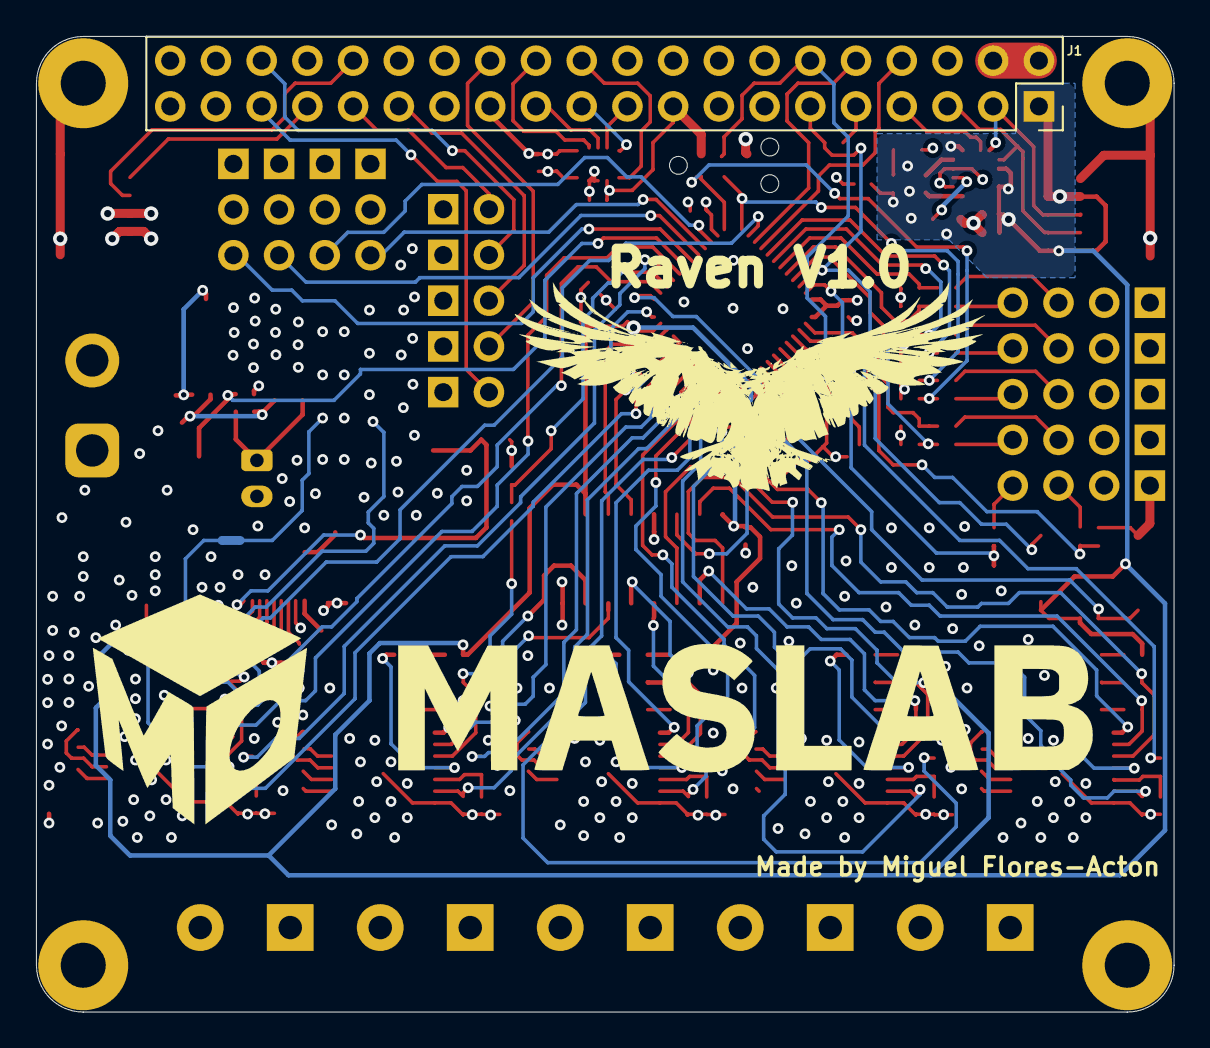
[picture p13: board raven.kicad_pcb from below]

Board: 4 copper layers, 63.2 x 54.2 mm, 198 parts (4 on the bottom side), 150 nets.

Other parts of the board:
G1, G2: LOGO

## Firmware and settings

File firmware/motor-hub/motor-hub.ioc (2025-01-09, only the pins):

Mcu.UserName=STM32G431CBUx
PA0.Signal=ADC1_IN1
PA1.Signal=S_TIM2_CH2
PA10.Signal=S_TIM1_CH3
PA11.Signal=S_TIM1_CH4
PA12.Signal=S_TIM16_CH1
PA13.GPIO_Label=B3
PA13.Signal=GPIO_Input
PA14.GPIO_Label=A3
PA14.Signal=GPIO_Input
PA15.GPIO_Label=SL5
PA15.Signal=GPIO_Output
PA2.Signal=S_TIM2_CH3
PA3.Signal=S_TIM2_CH4
PA4.Signal=ADC2_IN17
PA5.Signal=S_TIM2_CH1
PA6.Signal=S_TIM3_CH1
PA7.Signal=ADC2_IN4
PA8.GPIO_Label=PWR
PA8.Signal=GPIO_Output
PA9.Signal=S_TIM1_CH2
PB0.Signal=S_TIM3_CH3
PB1.Signal=S_TIM3_CH4
PB10.GPIO_Label=RSV
PB10.Signal=GPIO_Output
PB11.GPIO_Label=RCLK
PB11.Signal=GPIO_Output
PB12.GPIO_Label=RDAT
PB12.Signal=GPIO_Output
PB13.GPIO_Label=PH5
PB13.Signal=GPIO_Output
PB14.Signal=ADC1_IN5
PB15.Signal=S_TIM15_CH2
PB2.Signal=ADC2_IN12
PB3.GPIO_Label=B2
PB3.Signal=GPIO_Input
PB4.GPIO_Label=A2
PB4.Signal=GPIO_Input
PB5.GPIO_Label=A1
PB5.Signal=GPIO_Input
PB6.GPIO_Label=B1
PB6.Signal=GPIO_Input
PB7.GPIO_Label=B4
PB7.Signal=GPIO_Input
PB9.Signal=S_TIM4_CH4
PC10.Signal=USART3_TX
PC11.Signal=USART3_RX
PC13.GPIO_Label=A4
PC13.Signal=GPIO_Input
PC14-OSC32_IN.GPIO_Label=A5
PC14-OSC32_IN.Signal=GPIO_Input
PC15-OSC32_OUT.GPIO_Label=B5
PC15-OSC32_OUT.Signal=GPIO_Input
PC4.Signal=ADC2_IN5
PC6.Signal=S_TIM8_CH1
PF0-OSC_IN.Signal=RCC_OSC_IN
PF1-OSC_OUT.Signal=RCC_OSC_OUT

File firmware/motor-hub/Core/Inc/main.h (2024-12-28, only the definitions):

#define A4_Pin GPIO_PIN_13
#define A4_GPIO_Port GPIOC
#define A5_Pin GPIO_PIN_14
#define A5_GPIO_Port GPIOC
#define B5_Pin GPIO_PIN_15
#define B5_GPIO_Port GPIOC
#define RSV_Pin GPIO_PIN_10
#define RSV_GPIO_Port GPIOB
#define RCLK_Pin GPIO_PIN_11
#define RCLK_GPIO_Port GPIOB
#define RDAT_Pin GPIO_PIN_12
#define RDAT_GPIO_Port GPIOB
#define PH5_Pin GPIO_PIN_13
#define PH5_GPIO_Port GPIOB
#define PWR_Pin GPIO_PIN_8
#define PWR_GPIO_Port GPIOA
#define B3_Pin GPIO_PIN_13
#define B3_GPIO_Port GPIOA
#define A3_Pin GPIO_PIN_14
#define A3_GPIO_Port GPIOA
#define SL5_Pin GPIO_PIN_15
#define SL5_GPIO_Port GPIOA
#define B2_Pin GPIO_PIN_3
#define B2_GPIO_Port GPIOB
#define A2_Pin GPIO_PIN_4
#define A2_GPIO_Port GPIOB
#define A1_Pin GPIO_PIN_5
#define A1_GPIO_Port GPIOB
#define B1_Pin GPIO_PIN_6
#define B1_GPIO_Port GPIOB
#define B4_Pin GPIO_PIN_7
#define B4_GPIO_Port GPIOB

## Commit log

2024-10-23 Set up project
    [raven.kicad_pcb, raven.kicad_sch]
2024-10-24 Add rough schematic layout
    [encoder.kicad_sch, imu.kicad_sch, large-motor.kicad_sch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]
2024-10-25 Remove sensor hub
    [encoder.kicad_sch, imu.kicad_sch, large-motor.kicad_sch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]
2024-10-25 Finish schematic
    [encoder.kicad_sch, imu.kicad_sch, large-motor.kicad_sch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]
2024-10-26 Save progress
    [SM04B-SRSS-TB.STEP, encoder.kicad_sch, large-motor.kicad_sch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]
2024-10-29 Add another qwic connector
    [raven.kicad_sch]
2024-11-04 Finish first draft schematic
    [XT30PW-M.STEP, encoder.kicad_sch, motor-hub.kicad_sch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]
2024-11-05 Start on regulator
    [raven.kicad_pcb, raven.kicad_sch]
2024-11-12 Start wiring
    [large-motor.kicad_sch, motor-hub.kicad_sch, raven.kicad_pcb]
2024-11-13 Finish zones
    [raven.kicad_pcb]
2024-11-15 Add new regulator info
    [raven.kicad_sch]
2024-11-15 Remove regulator
    [raven.kicad_sch]
2024-11-18 Finish lipo shutdown
    [XT30UPB-M.STEP, motor-hub.kicad_sch, raven.kicad_pcb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]
2024-11-19 Finish routing
    [motor-hub.kicad_sch, raven.kicad_pcb, raven.kicad_sch]
2024-11-19 Pass drc
    [raven.kicad_pcb]
2024-11-19 Add silkscreen
    [raven.kicad_pcb]
2024-11-19 Change cutoff voltage
    [raven.kicad_pcb, raven.kicad_sch]
2024-11-21 Verify production files
    [bom.csv, designators.csv, positions.csv]
2024-11-23 Plan adding power switch
    [imu.kicad_sch, raven.kicad_pcb, raven.kicad_sch]
2024-11-25 Add power switch
    [bom.csv, designators.csv, encoder.kicad_sch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]
2024-12-11 Finish for revision 2 production
    [bom.csv, designators.csv, encoder.kicad_sch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]
2024-12-11 Add vsense kelvin connections
    [designators.csv, positions.csv, raven.kicad_pcb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]
2024-12-26 Config periferals
    [raven.kicad_pcb]
2025-01-01 Fix crc error and use void for message
    [app.c, com.c]
2025-01-03 Fix voltage signedness
2025-01-06 Fix timer and parser
    [app.c, motor-hub.ioc]
2025-01-06 Add velocity read command
2025-01-06 Change timer prescalar
2025-01-06 Init parser and correct target type
    [app.c]
2025-01-06 Fix motor enable
2025-01-07 Not blocking transmit, use IT instead of DMA, and process 1 encoder at a time
2025-01-10 Add software reset and watchdog
    [app.c]
2025-01-10 Only reset encoder if reset with reset command
    [app.c]
2025-01-10 Keeps motor enabled but reset PID and not handle PID when timeout
    [app.c]
2025-01-11 Tune parameters for PID
2025-01-15 Remove reinit PID
2025-11-11 Fix encoder pull downs
    [encoder.kicad_sch, imu.kicad_sch, large-motor.kicad_sch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]
2025-11-26 Update production files
    [bom.csv, positions.csv, raven.kicad_pcb]

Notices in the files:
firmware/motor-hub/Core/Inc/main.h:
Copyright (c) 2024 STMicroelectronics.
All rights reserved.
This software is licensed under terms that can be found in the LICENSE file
